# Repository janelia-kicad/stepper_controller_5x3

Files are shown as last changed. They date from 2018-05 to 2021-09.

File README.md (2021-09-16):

- [Repository Information](#org1390894)
  - [Description](#org5e8a07c)
- [Images](#org5d62455)
- [Schematic](#org4a582db)
- [Gerbers](#org312467b)
- [Bill of Materials](#org7a5552a)
  - [PCB Parts](#orgf9d748f)
  - [Supplemental Parts](#orgd5227c2)
  - [Vendor Parts Lists](#org4a799e8)
- [Supplemental Documentation](#org5107894)
  - [Assembly Instructions](#org090c8bb)

# Repository Information

-   **Name:** stepper\_controller\_5x3
-   **Version:** 1.3
-   **License:** Open-Source Hardware
-   **URL:** <https://github.com/janelia-kicad/stepper_controller_5x3>
-   **Author:** Peter Polidoro
-   **Email:** peter@polidoro.io

## Description

This board controls up to 3 stepper motors with optional forward and reverse limit switches for each motor.

# Images

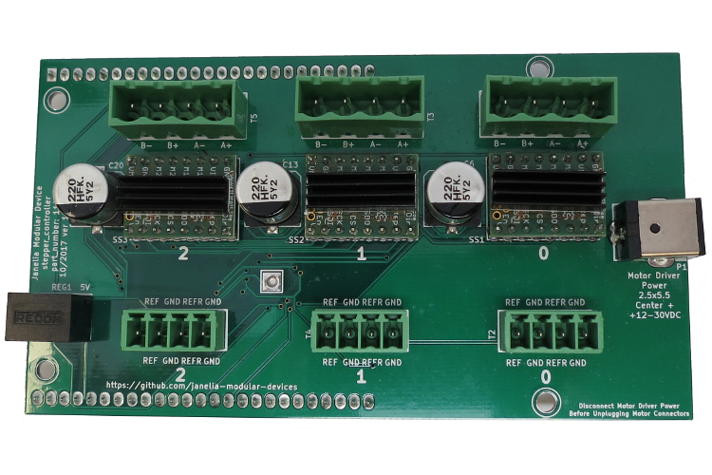
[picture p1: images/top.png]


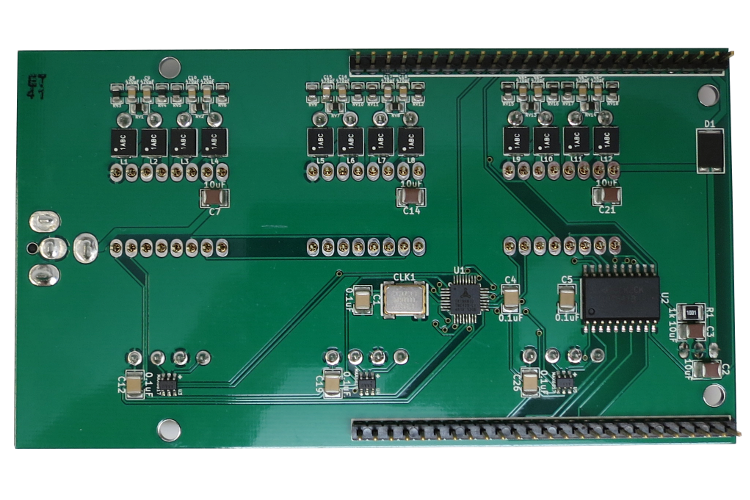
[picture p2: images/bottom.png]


# Schematic

[./schematic/stepper\_controller\_5x3.pdf](./schematic/stepper_controller_5x3.pdf)

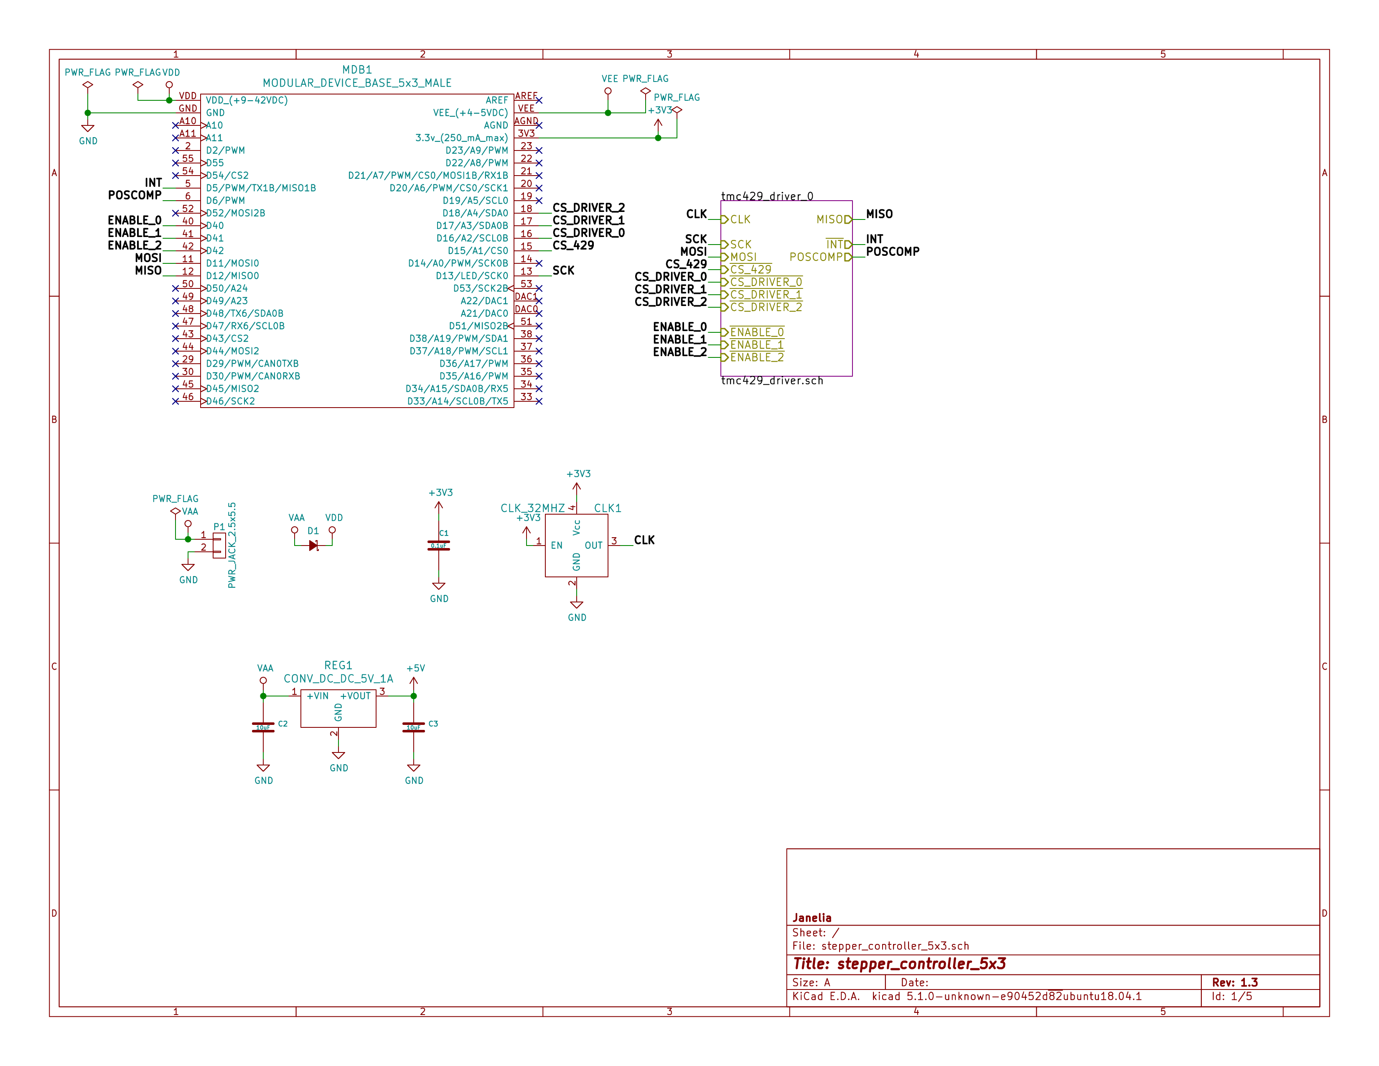
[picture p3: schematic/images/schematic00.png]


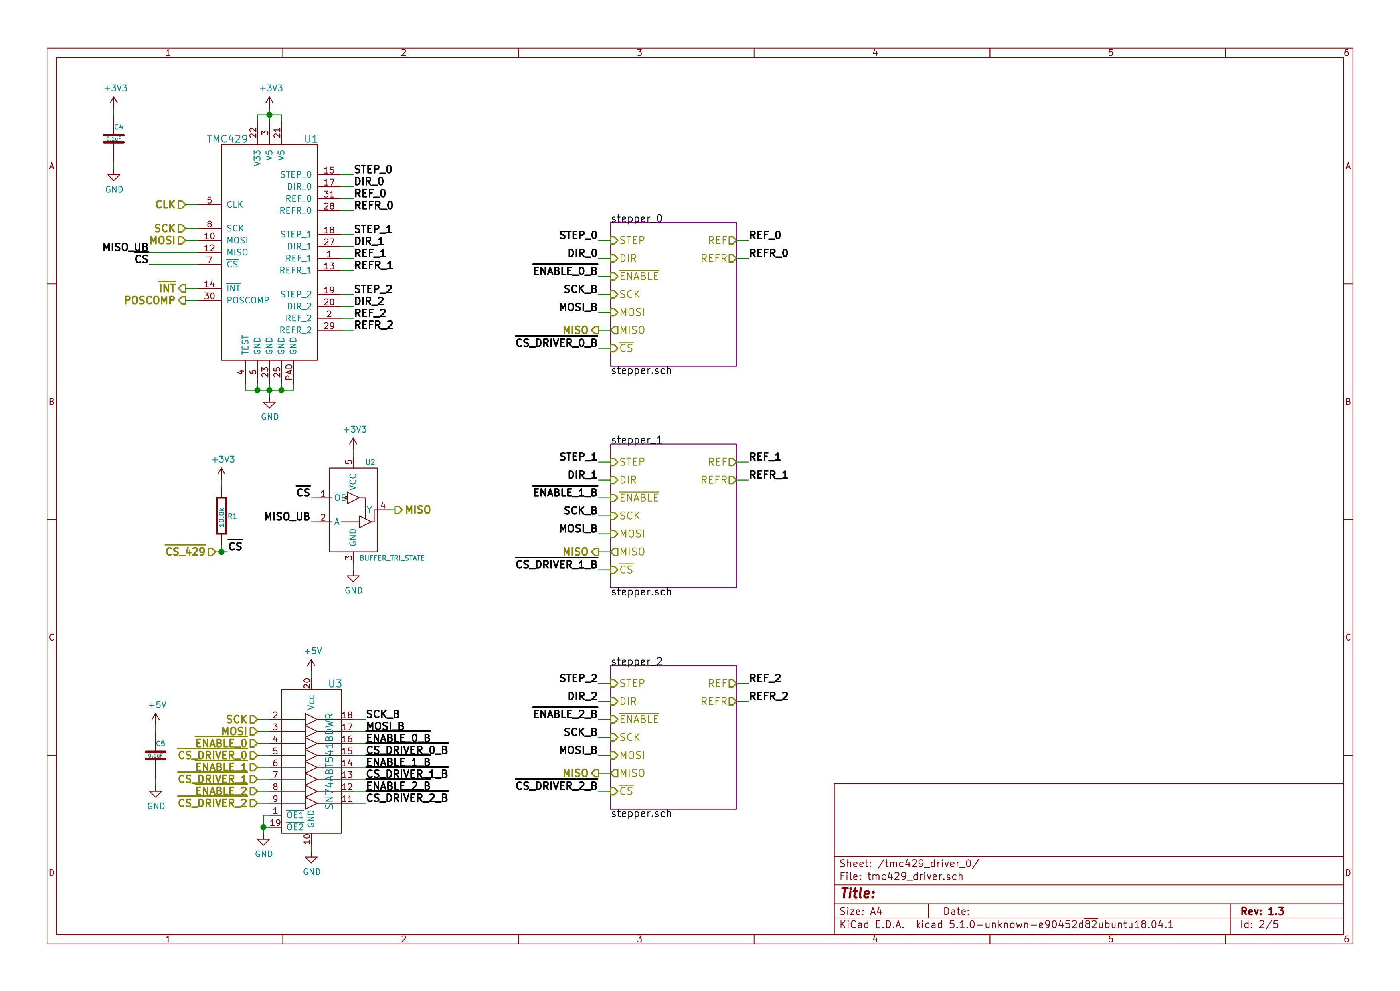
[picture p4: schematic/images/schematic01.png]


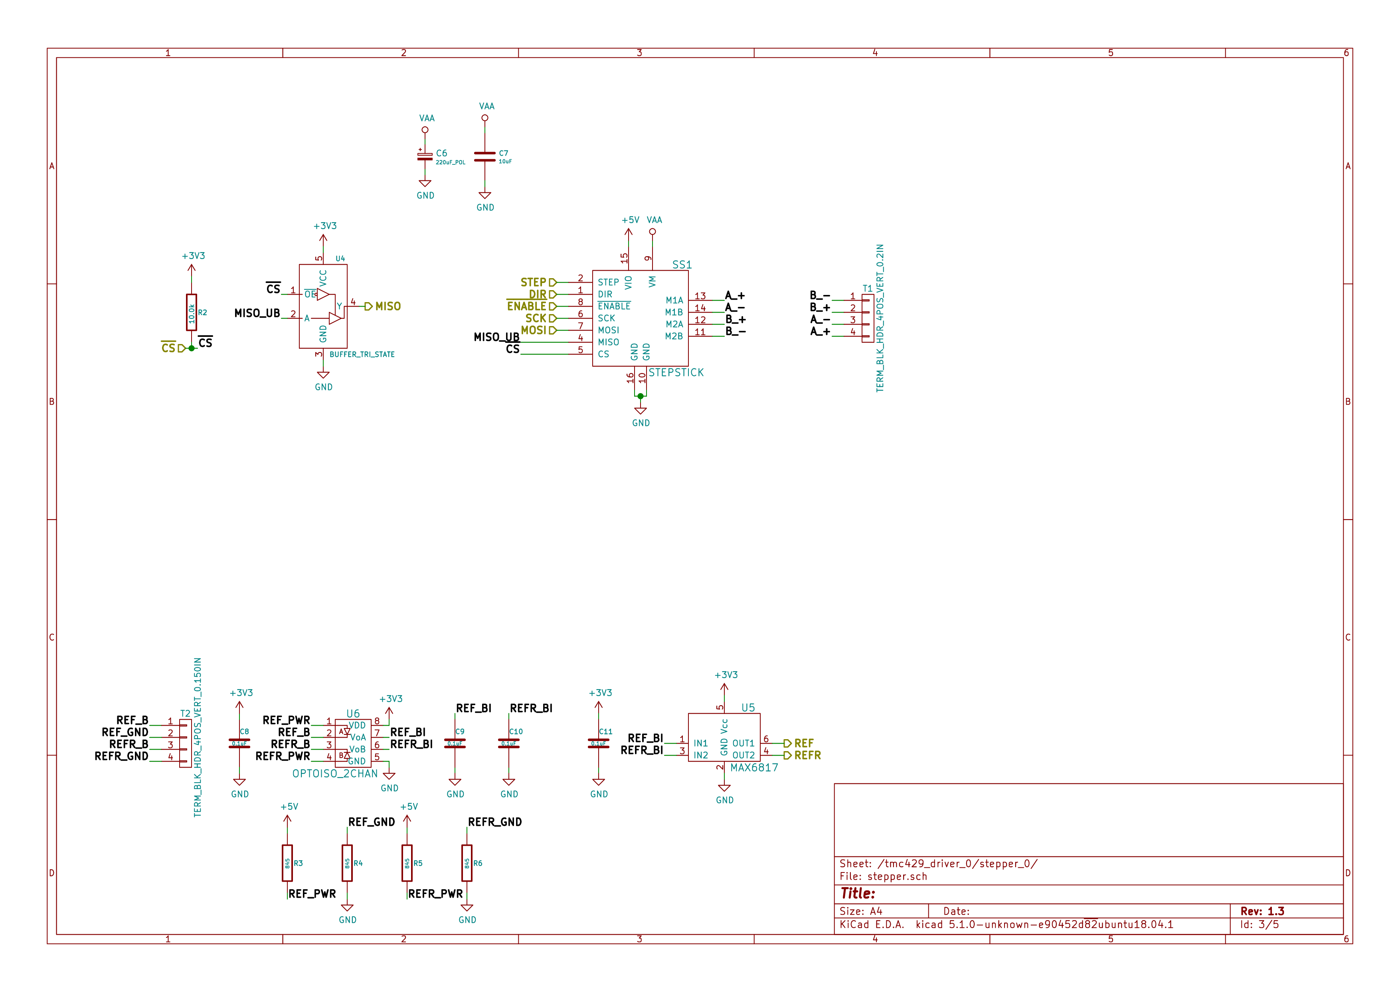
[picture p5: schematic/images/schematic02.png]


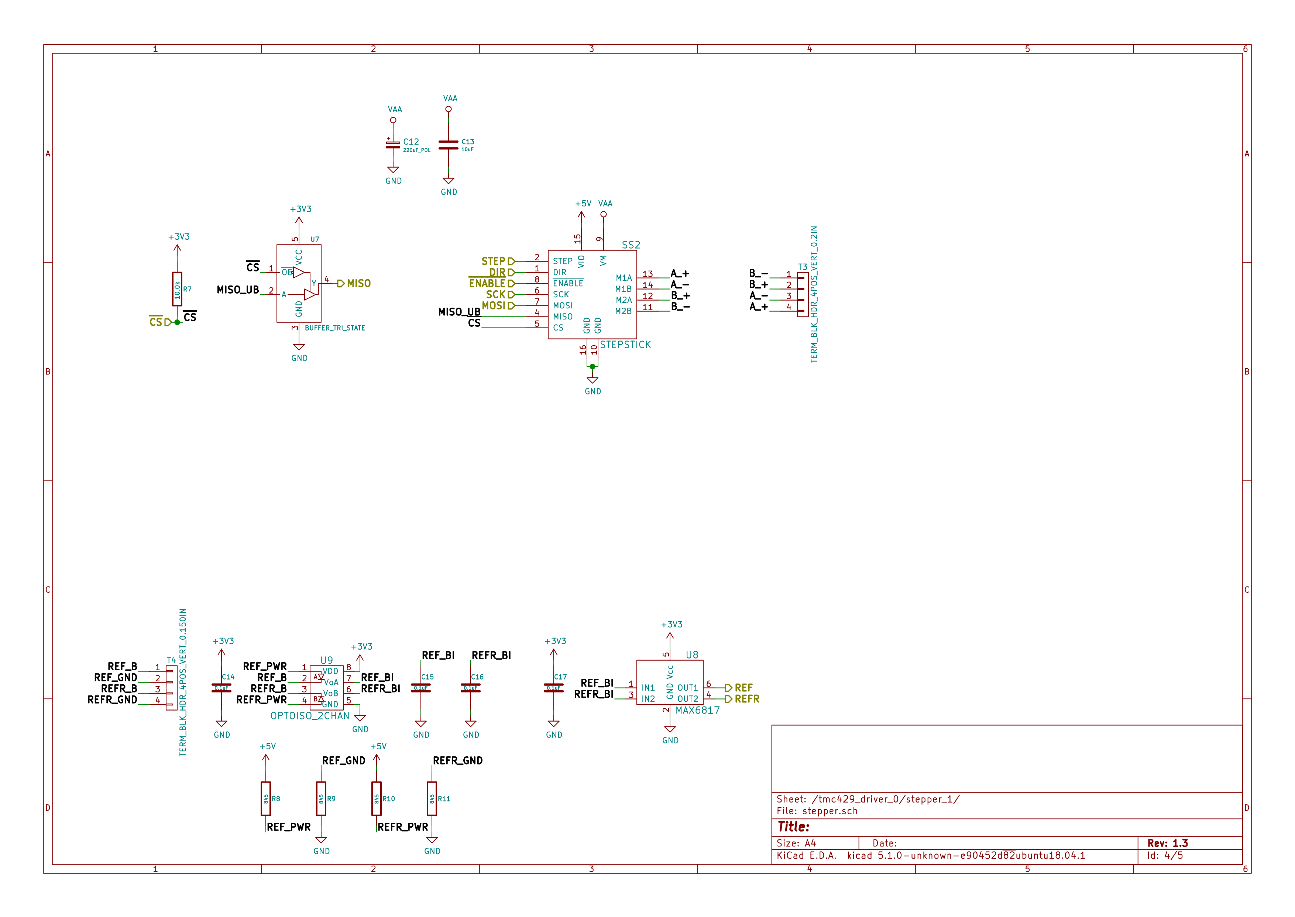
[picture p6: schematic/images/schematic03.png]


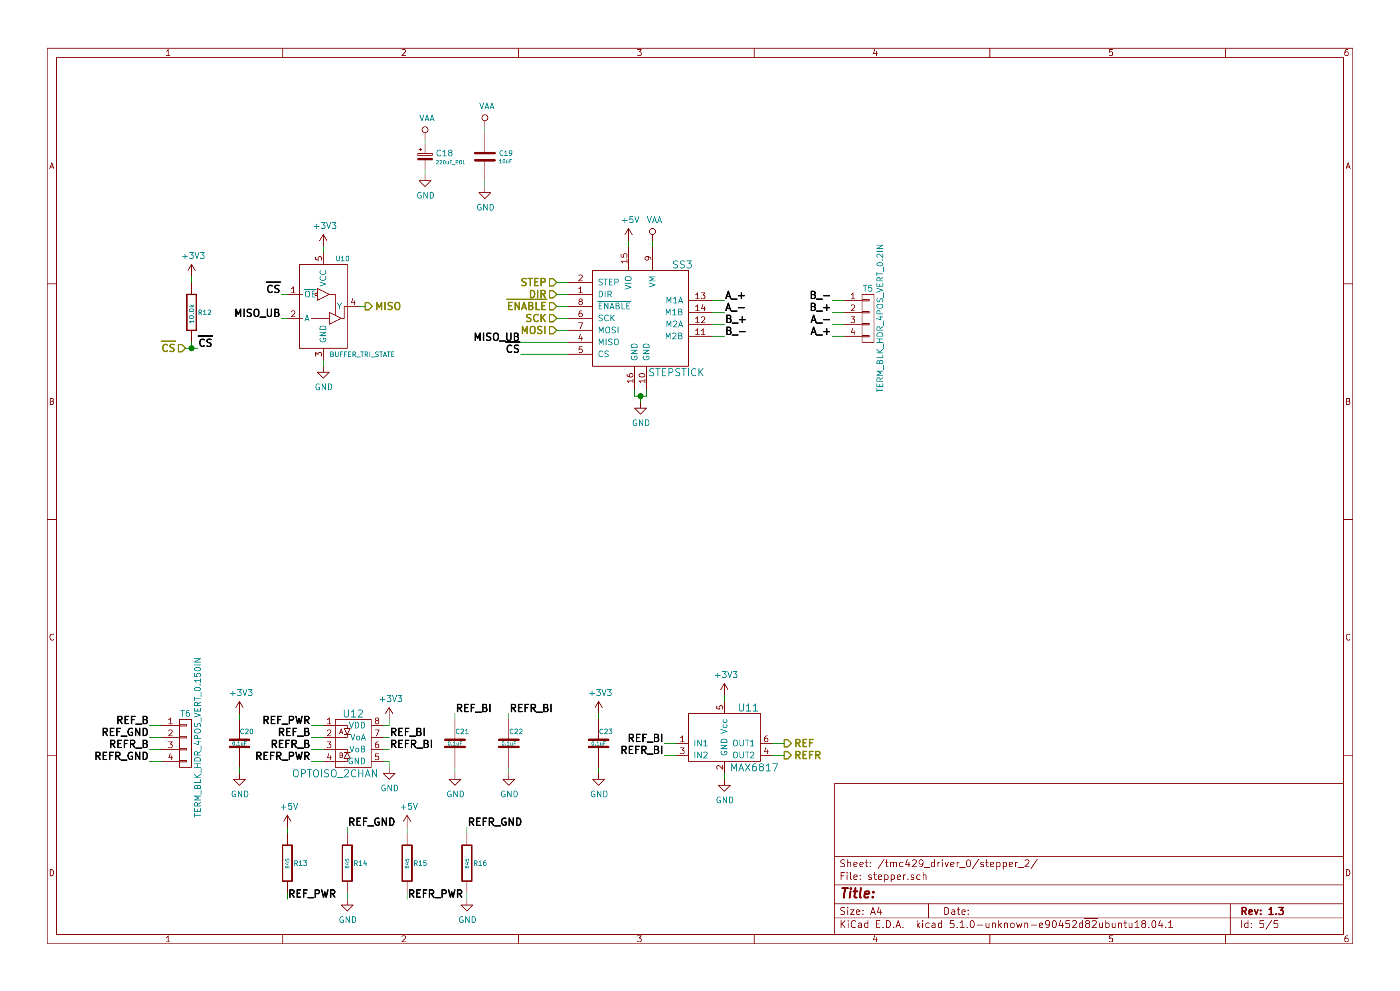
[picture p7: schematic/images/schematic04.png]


# Gerbers

Send gerbers zip file to your favorite PCB manufacturer for fabrication.

[./gerbers/stepper\_controller\_5x3\_v1.3.zip](./gerbers/stepper_controller_5x3_v1.3.zip)

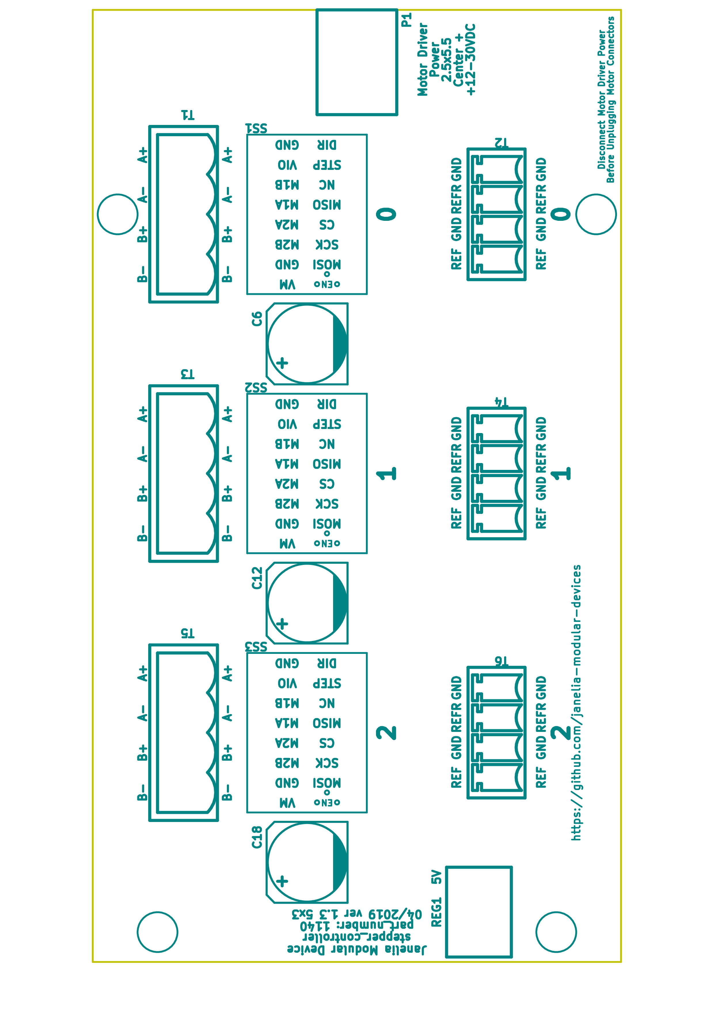
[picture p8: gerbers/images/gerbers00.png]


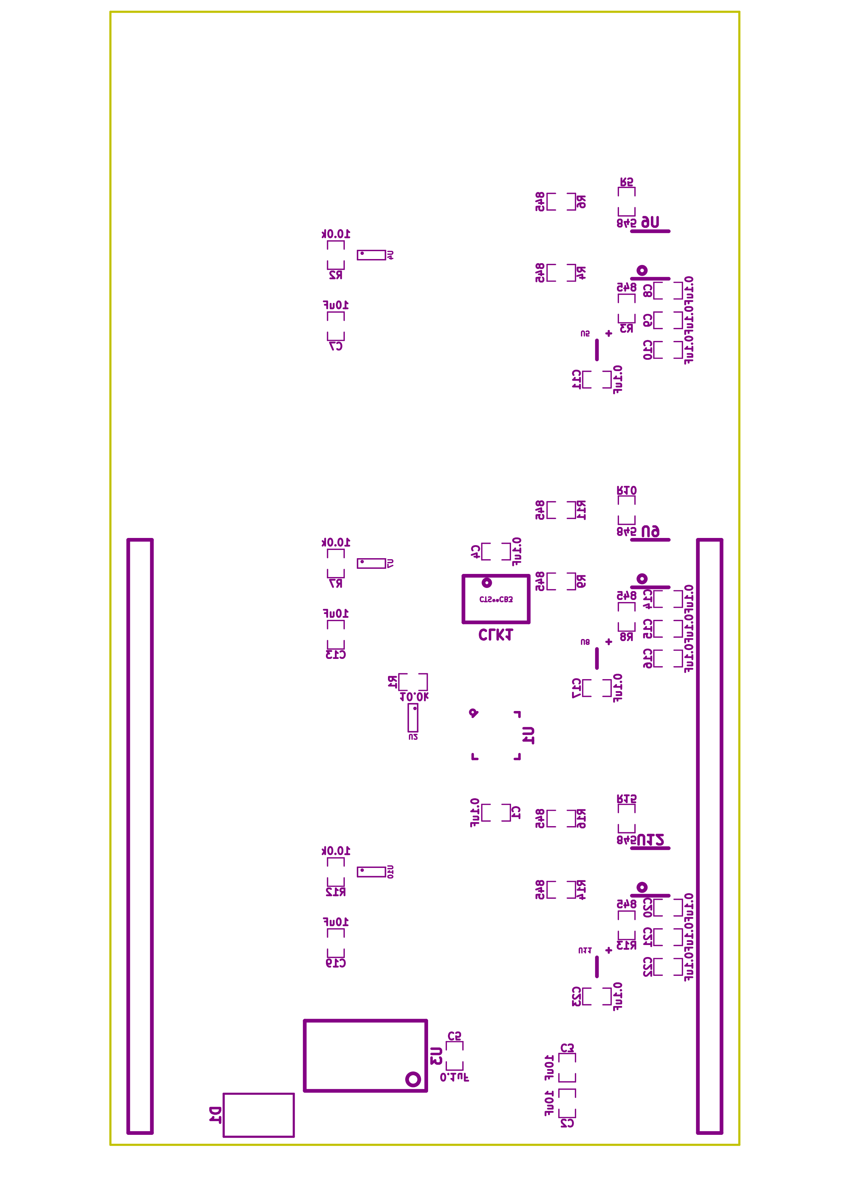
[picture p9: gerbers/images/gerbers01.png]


# Bill of Materials

## PCB Parts

| Item | Reference(s) | Quantity | PartNumber | Vendor  | Description |
|---- |--- |--- |--- |--- |--- |
| 1 | C1 C10 C11 C14 C15 C16 C17 C20 C21 C22 C23 C4 C5 C8 C9 | 15 | 399-14636-1-ND | digikey | CAP CER 0.1UF 50V X7R 0805 |
| 2 | C12 C18 C6 | 3 | PCE3812CT-ND | digikey | CAP ALUM 220UF 20% 50V SMD |
| 3 | C13 C19 C2 C3 C7 | 5 | 445-14419-1-ND | digikey | CAP CER 10UF 35V X5R 0805 |
| 4 | CLK1 | 1 | CTX277LVCT-ND | digikey | OSC XO 32.000MHZ HCMOS TTL SMD |
| 5 | D1 | 1 | 568-11697-1-ND | digikey | DIODE SCHOTTKY 45V 10A CFP15 |
| 6 | MDB1 | 2 | S1011E-25-ND | digikey | 25 Positions Header Breakaway Connector 0.1in |
| 7 | P1 | 1 | CP-063BH-ND | digikey | CONN PWR JACK DC 2.5X5.5 8A T/H |
| 8 | R1 R12 R2 R7 | 4 | P10.0KCCT-ND | digikey | RES SMD 10K OHM 1% 1/8W 0805 |
| 9 | R10 R11 R13 R14 R15 R16 R3 R4 R5 R6 R8 R9 | 12 | P845CCT-ND | digikey | RES SMD 845 OHM 1% 1/8W 0805 |
| 10 | REG1 | 1 | 945-1395-5-ND | digikey | CONV DC/DC 1A 5V OUT SIP VERT |
| 11 | SS1 SS2 SS3 | 48 | ED90331-ND | digikey | CONN PIN RCPT .025-.037 SOLDER |
| 12 | T1 T3 T5 | 3 | 277-1152-ND | digikey | TERM BLOCK HDR 4POS VERT 5.08MM |
| 13 | T2 T4 T6 | 3 | 277-1223-ND | digikey | TERM BLOCK HDR 4POS VERT 3.81MM |
| 14 | U1 | 1 | 1460-1071-1-ND | digikey | IC MOTOR CONTROLLER SPI 32QFN |
| 15 | U10 U2 U4 U7 | 4 | 296-11603-1-ND | digikey | IC BUF NON-INVERT 5.5V SOT23-5 |
| 16 | U11 U5 U8 | 3 | MAX6817EUT+TCT-ND | digikey | IC DEBOUNCER SWITCH DUAL SOT23-6 |
| 17 | U12 U6 U9 | 3 | 516-2614-1-ND | digikey | OPTOISO 3.75KV 2CH PUSH PULL 8SO |
| 18 | U3 | 1 | 296-14668-1-ND | digikey | Buffer Non-Inverting 1 Element 8 Bit per Element Push-Pull Output 20-SOIC |

## Supplemental Parts

| Item | Quantity | PartNumber | Vendor  | Description |
|---- |--- |--- |--- |--- |
| 1 | 3 | 277-1013-ND | digikey | TERM BLOCK PLUG 4POS STR 5.08MM |
| 2 | 3 | 277-1042-ND | digikey | TERM BLOCK PLUG 4POS 5.08MM |
| 3 | 3 | 277-1163-ND | digikey | TERM BLOCK PLUG 4POS STR 3.81MM |
| 4 | 3 | 277-1193-ND | digikey | TERM BLOCK PLUG 4POS 90DEG 3.81MM |
| 5 | 3 | 1460-1187-ND | digikey | TMC2130 STEPPER DRIVER BOARD |
| 6 | 3 | 501100B00000G-ND | digikey | HEATSINK 14-DIP/16-DIP |
| 7 | 1 | 3M10315-ND | digikey | TAPE ADHESIVE TRANSFER 1/2in X5YD |

## Vendor Parts Lists

[./bom/digikey\_parts.csv](./bom/digikey_parts.csv)

[./bom/supplemental\_digikey\_parts.csv](./bom/supplemental_digikey_parts.csv)

# Supplemental Documentation

## Assembly Instructions

-   Solder header pins into the stepper driver board(s), making note of TOP label. Insert header pins on bottom of board so that the long unsoldered header pins point down when the TOP label faces up.
-   Expose one side of the thermal adhesive tape and attach to the bottom of the heatsink. Trim tape so it does not extend beyond heatsink edges.
-   Expose the other side of the thermal adhesive tape and attach the heatsink to the stepper driver board on the side with the TOP label.
-   Solder surface mount and through hole components onto the pcb.
-   Insert stepper driver board(s) into pin receptacles.

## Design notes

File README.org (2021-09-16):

# Created 2019-04-11 Thu 14:58
#+OPTIONS: title:nil author:nil email:nil toc:t |:t ^:nil
* Repository Information

- Name :: stepper_controller_5x3
- Version :: 1.3
- License :: Open-Source Hardware
- URL :: https://github.com/janelia-kicad/stepper_controller_5x3
- Author :: Peter Polidoro
- Email :: peter@polidoro.io

** Description

This board controls up to 3 stepper motors with optional forward and reverse
limit switches for each motor.

* Images





* Schematic

[[file:./schematic/stepper_controller_5x3.pdf][./schematic/stepper_controller_5x3.pdf]]











* Gerbers

Send gerbers zip file to your favorite PCB manufacturer for fabrication.

[[file:./gerbers/stepper_controller_5x3_v1.3.zip][./gerbers/stepper_controller_5x3_v1.3.zip]]





* Bill of Materials

** PCB Parts

| Item | Reference(s)                                           | Quantity | PartNumber        | Vendor  | Description                                                               |
|------+--------------------------------------------------------+----------+-------------------+---------+---------------------------------------------------------------------------|
|    1 | C1 C10 C11 C14 C15 C16 C17 C20 C21 C22 C23 C4 C5 C8 C9 |       15 | 399-14636-1-ND    | digikey | CAP CER 0.1UF 50V X7R 0805                                                |
|    2 | C12 C18 C6                                             |        3 | PCE3812CT-ND      | digikey | CAP ALUM 220UF 20% 50V SMD                                                |
|    3 | C13 C19 C2 C3 C7                                       |        5 | 445-14419-1-ND    | digikey | CAP CER 10UF 35V X5R 0805                                                 |
|    4 | CLK1                                                   |        1 | CTX277LVCT-ND     | digikey | OSC XO 32.000MHZ HCMOS TTL SMD                                            |
|    5 | D1                                                     |        1 | 568-11697-1-ND    | digikey | DIODE SCHOTTKY 45V 10A CFP15                                              |
|    6 | MDB1                                                   |        2 | S1011E-25-ND      | digikey | 25 Positions Header Breakaway Connector 0.1in                             |
|    7 | P1                                                     |        1 | CP-063BH-ND       | digikey | CONN PWR JACK DC 2.5X5.5 8A T/H                                           |
|    8 | R1 R12 R2 R7                                           |        4 | P10.0KCCT-ND      | digikey | RES SMD 10K OHM 1% 1/8W 0805                                              |
|    9 | R10 R11 R13 R14 R15 R16 R3 R4 R5 R6 R8 R9              |       12 | P845CCT-ND        | digikey | RES SMD 845 OHM 1% 1/8W 0805                                              |
|   10 | REG1                                                   |        1 | 945-1395-5-ND     | digikey | CONV DC/DC 1A 5V OUT SIP VERT                                             |
|   11 | SS1 SS2 SS3                                            |       48 | ED90331-ND        | digikey | CONN PIN RCPT .025-.037 SOLDER                                            |
|   12 | T1 T3 T5                                               |        3 | 277-1152-ND       | digikey | TERM BLOCK HDR 4POS VERT 5.08MM                                           |
|   13 | T2 T4 T6                                               |        3 | 277-1223-ND       | digikey | TERM BLOCK HDR 4POS VERT 3.81MM                                           |
|   14 | U1                                                     |        1 | 1460-1071-1-ND    | digikey | IC MOTOR CONTROLLER SPI 32QFN                                             |
|   15 | U10 U2 U4 U7                                           |        4 | 296-11603-1-ND    | digikey | IC BUF NON-INVERT 5.5V SOT23-5                                            |
|   16 | U11 U5 U8                                              |        3 | MAX6817EUT+TCT-ND | digikey | IC DEBOUNCER SWITCH DUAL SOT23-6                                          |
|   17 | U12 U6 U9                                              |        3 | 516-2614-1-ND     | digikey | OPTOISO 3.75KV 2CH PUSH PULL 8SO                                          |
|   18 | U3                                                     |        1 | 296-14668-1-ND    | digikey | Buffer Non-Inverting 1 Element 8 Bit per Element Push-Pull Output 20-SOIC |

** Supplemental Parts

| Item | Quantity | PartNumber       | Vendor  | Description                       |
|------+----------+------------------+---------+-----------------------------------|
|    1 |        3 | 277-1013-ND      | digikey | TERM BLOCK PLUG 4POS STR 5.08MM   |
|    2 |        3 | 277-1042-ND      | digikey | TERM BLOCK PLUG 4POS 5.08MM       |
|    3 |        3 | 277-1163-ND      | digikey | TERM BLOCK PLUG 4POS STR 3.81MM   |
|    4 |        3 | 277-1193-ND      | digikey | TERM BLOCK PLUG 4POS 90DEG 3.81MM |
|    5 |        3 | 1460-1187-ND     | digikey | TMC2130 STEPPER DRIVER BOARD      |
|    6 |        3 | 501100B00000G-ND | digikey | HEATSINK 14-DIP/16-DIP            |
|    7 |        1 | 3M10315-ND       | digikey | TAPE ADHESIVE TRANSFER 1/2in X5YD |

** Vendor Parts Lists

[[file:./bom/digikey_parts.csv][./bom/digikey_parts.csv]]

[[file:./bom/supplemental_digikey_parts.csv][./bom/supplemental_digikey_parts.csv]]

* Supplemental Documentation

** Assembly Instructions

- Solder header pins into the stepper driver board(s), making note of TOP label.
  Insert header pins on bottom of board so that the long unsoldered header
  pins point down when the TOP label faces up.
- Expose one side of the thermal adhesive tape and attach to the bottom of the
  heatsink. Trim tape so it does not extend beyond heatsink edges.
- Expose the other side of the thermal adhesive tape and attach the heatsink
  to the stepper driver board on the side with the TOP label.
- Solder surface mount and through hole components onto the pcb.
- Insert stepper driver board(s) into pin receptacles.

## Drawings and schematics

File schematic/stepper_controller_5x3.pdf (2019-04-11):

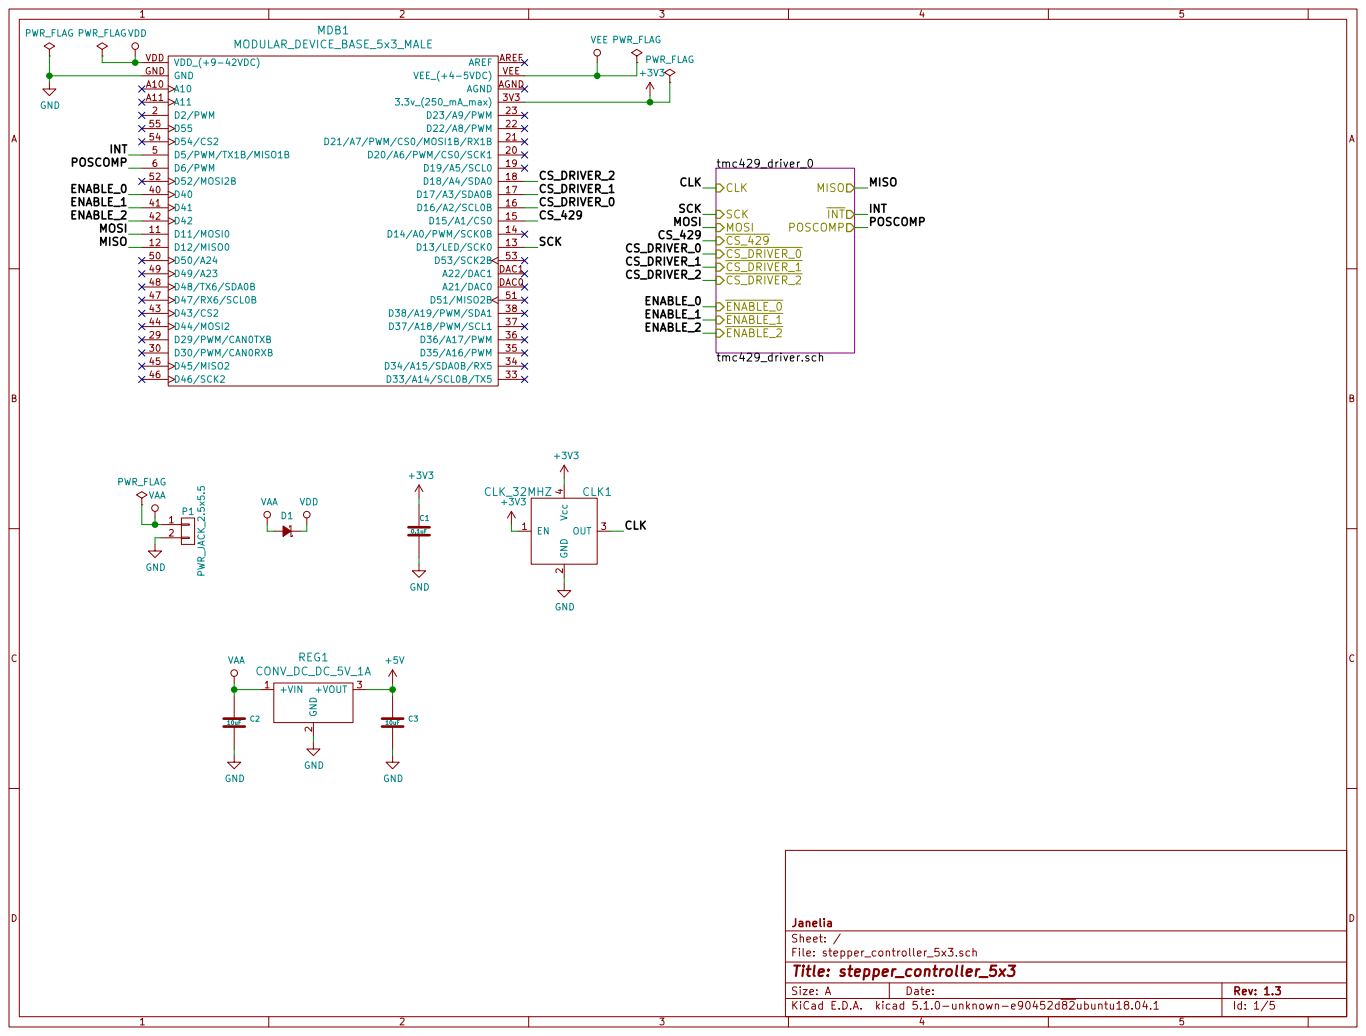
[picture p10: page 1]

File: stepper_controller_5x3.sch Sheet: / Janelia

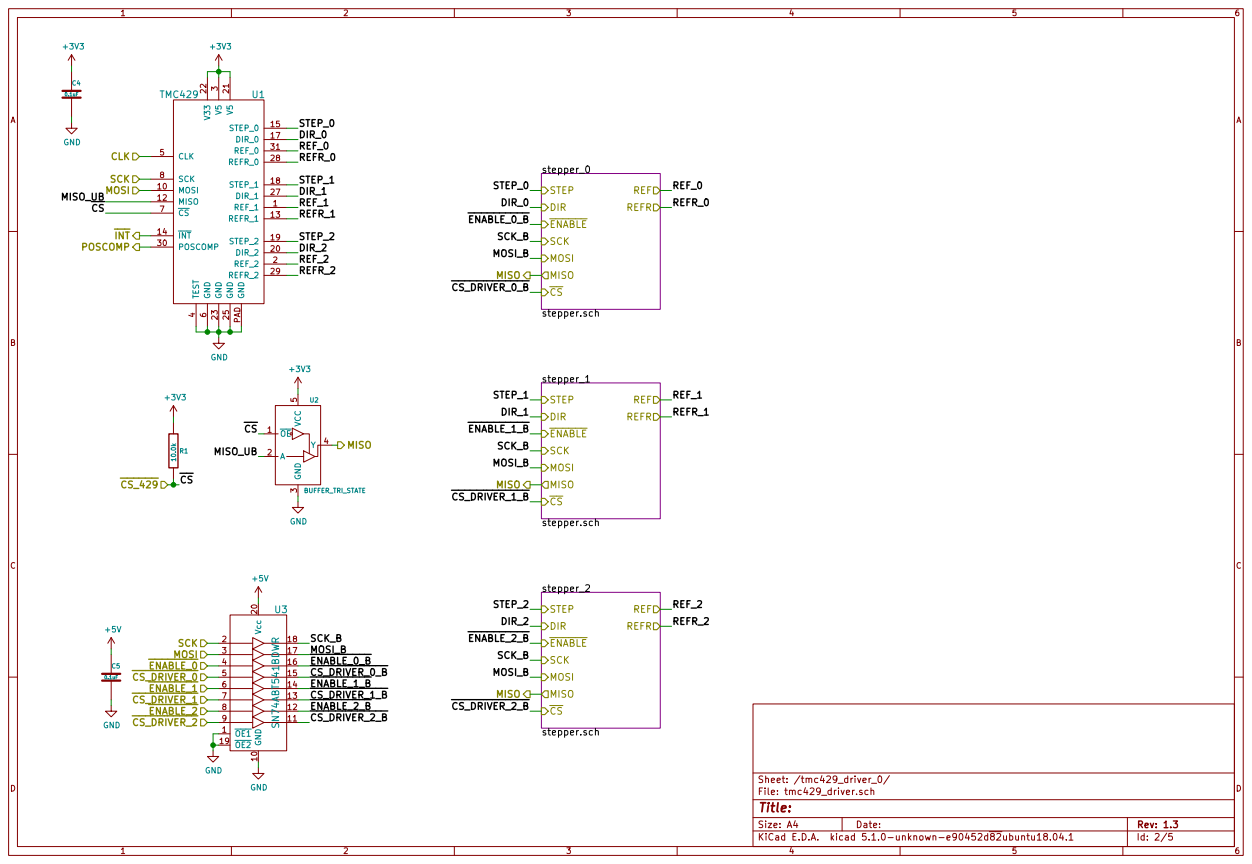
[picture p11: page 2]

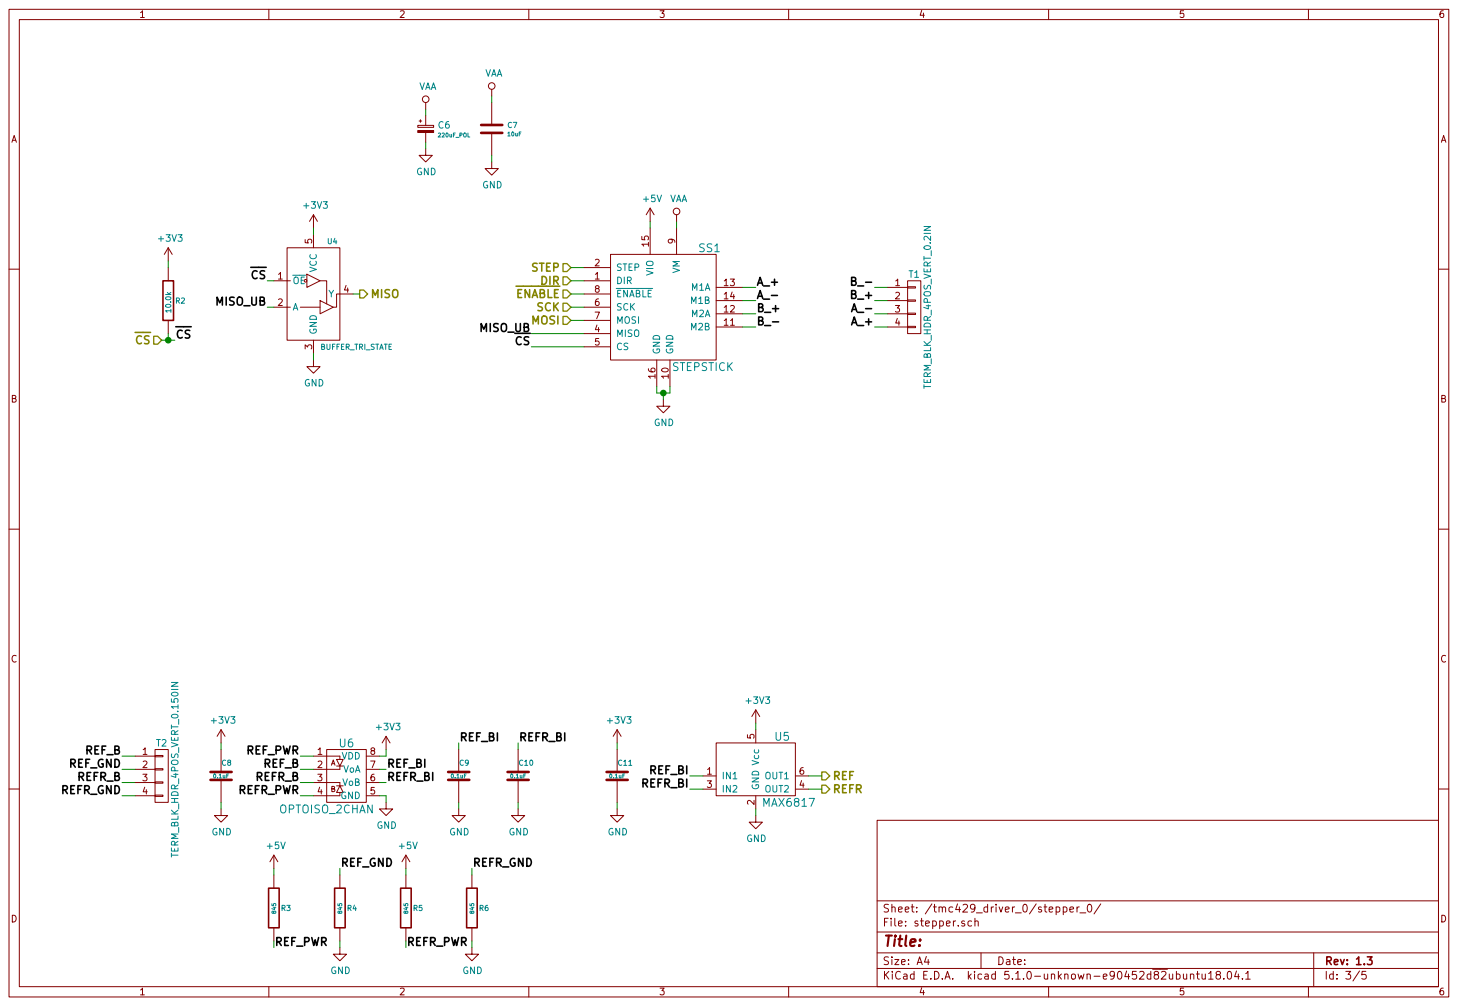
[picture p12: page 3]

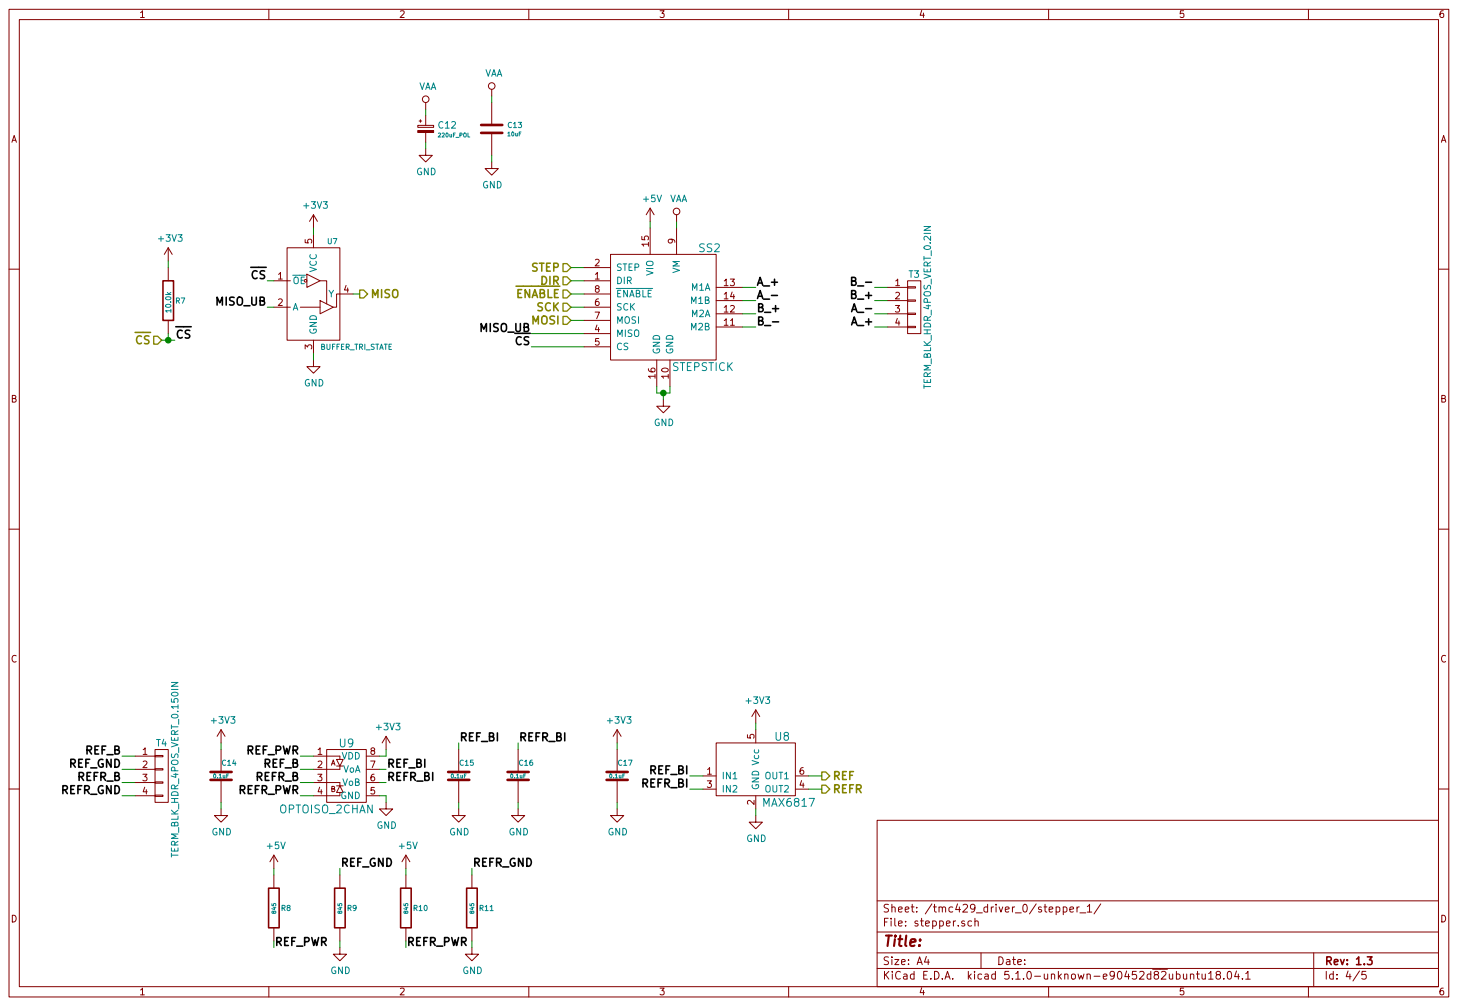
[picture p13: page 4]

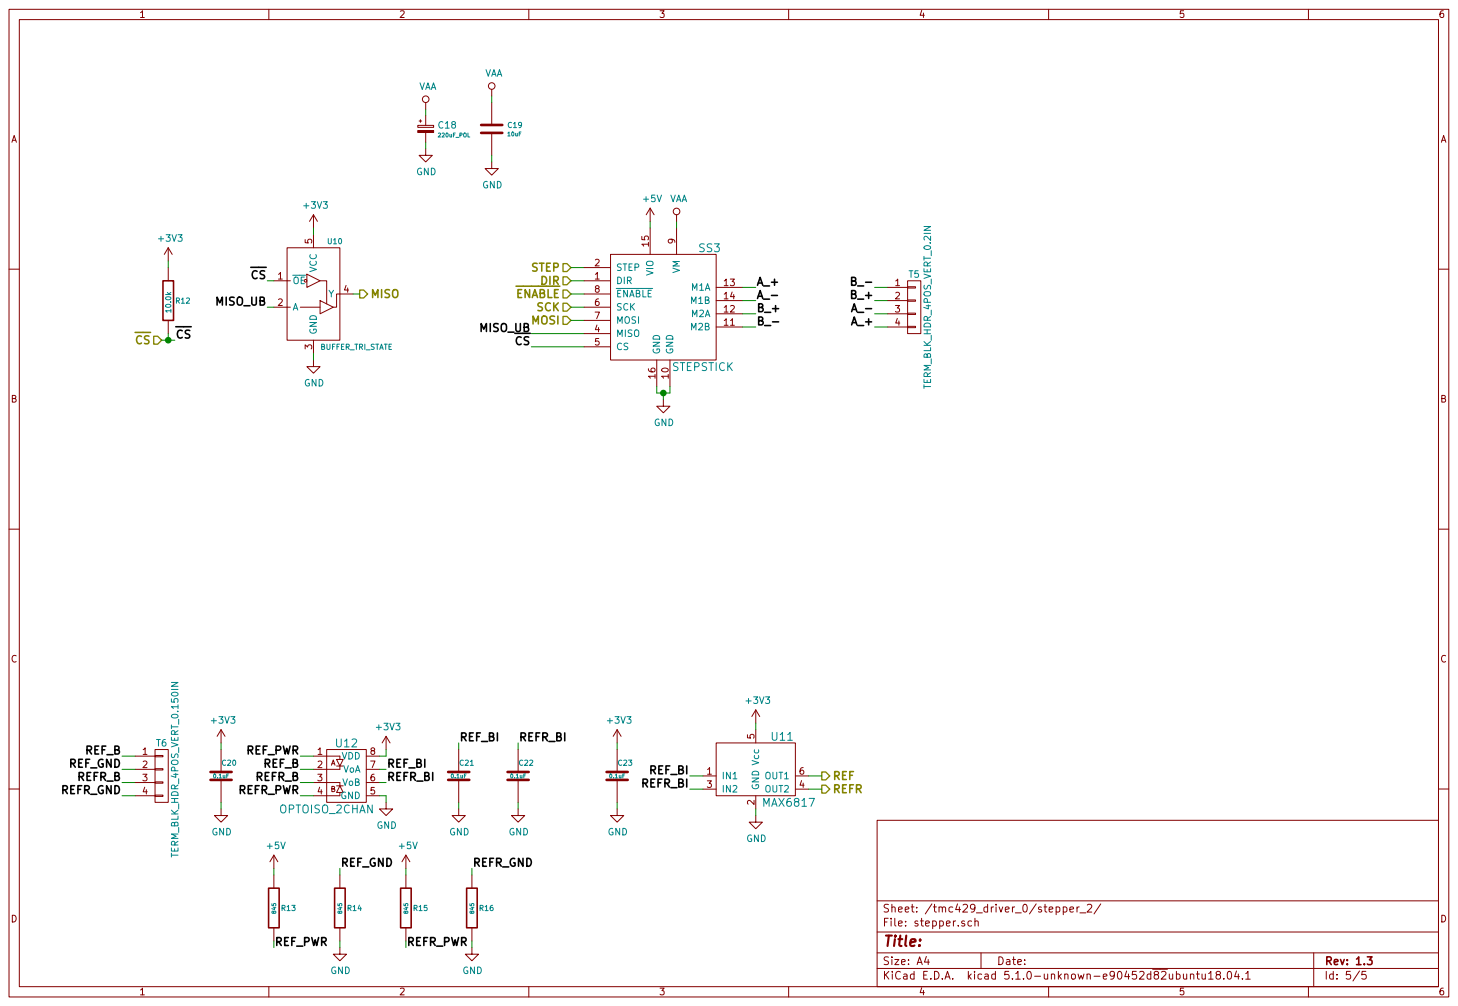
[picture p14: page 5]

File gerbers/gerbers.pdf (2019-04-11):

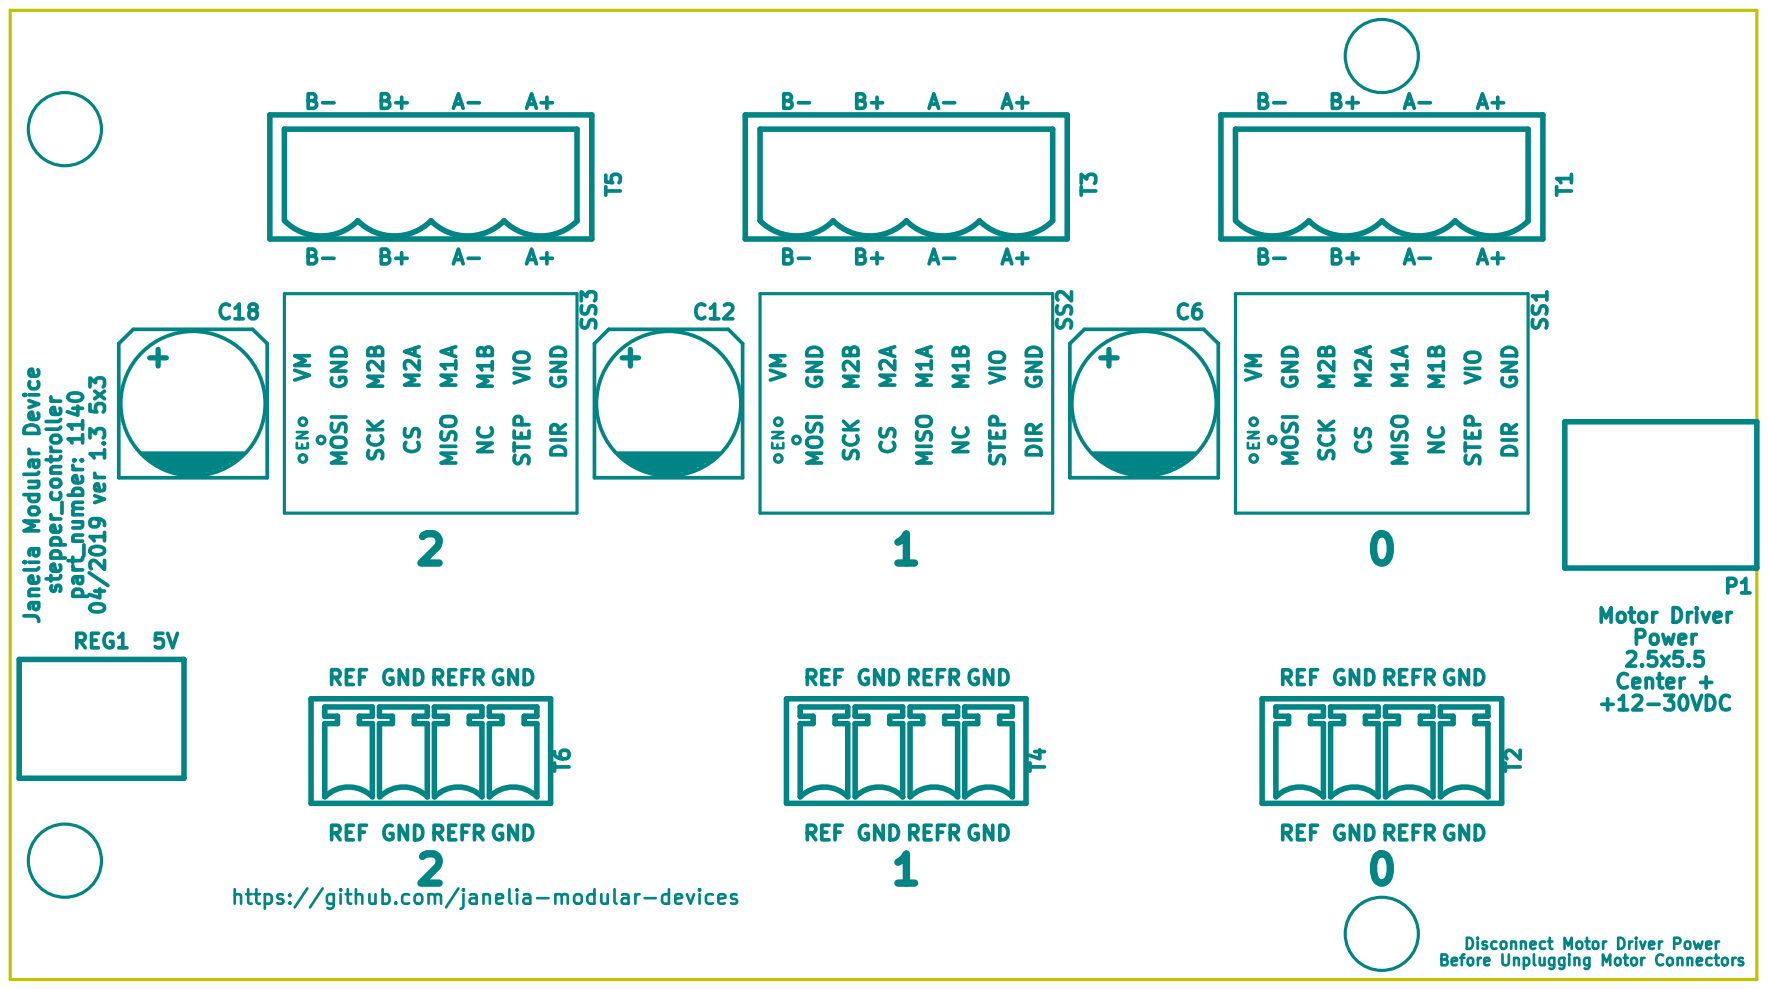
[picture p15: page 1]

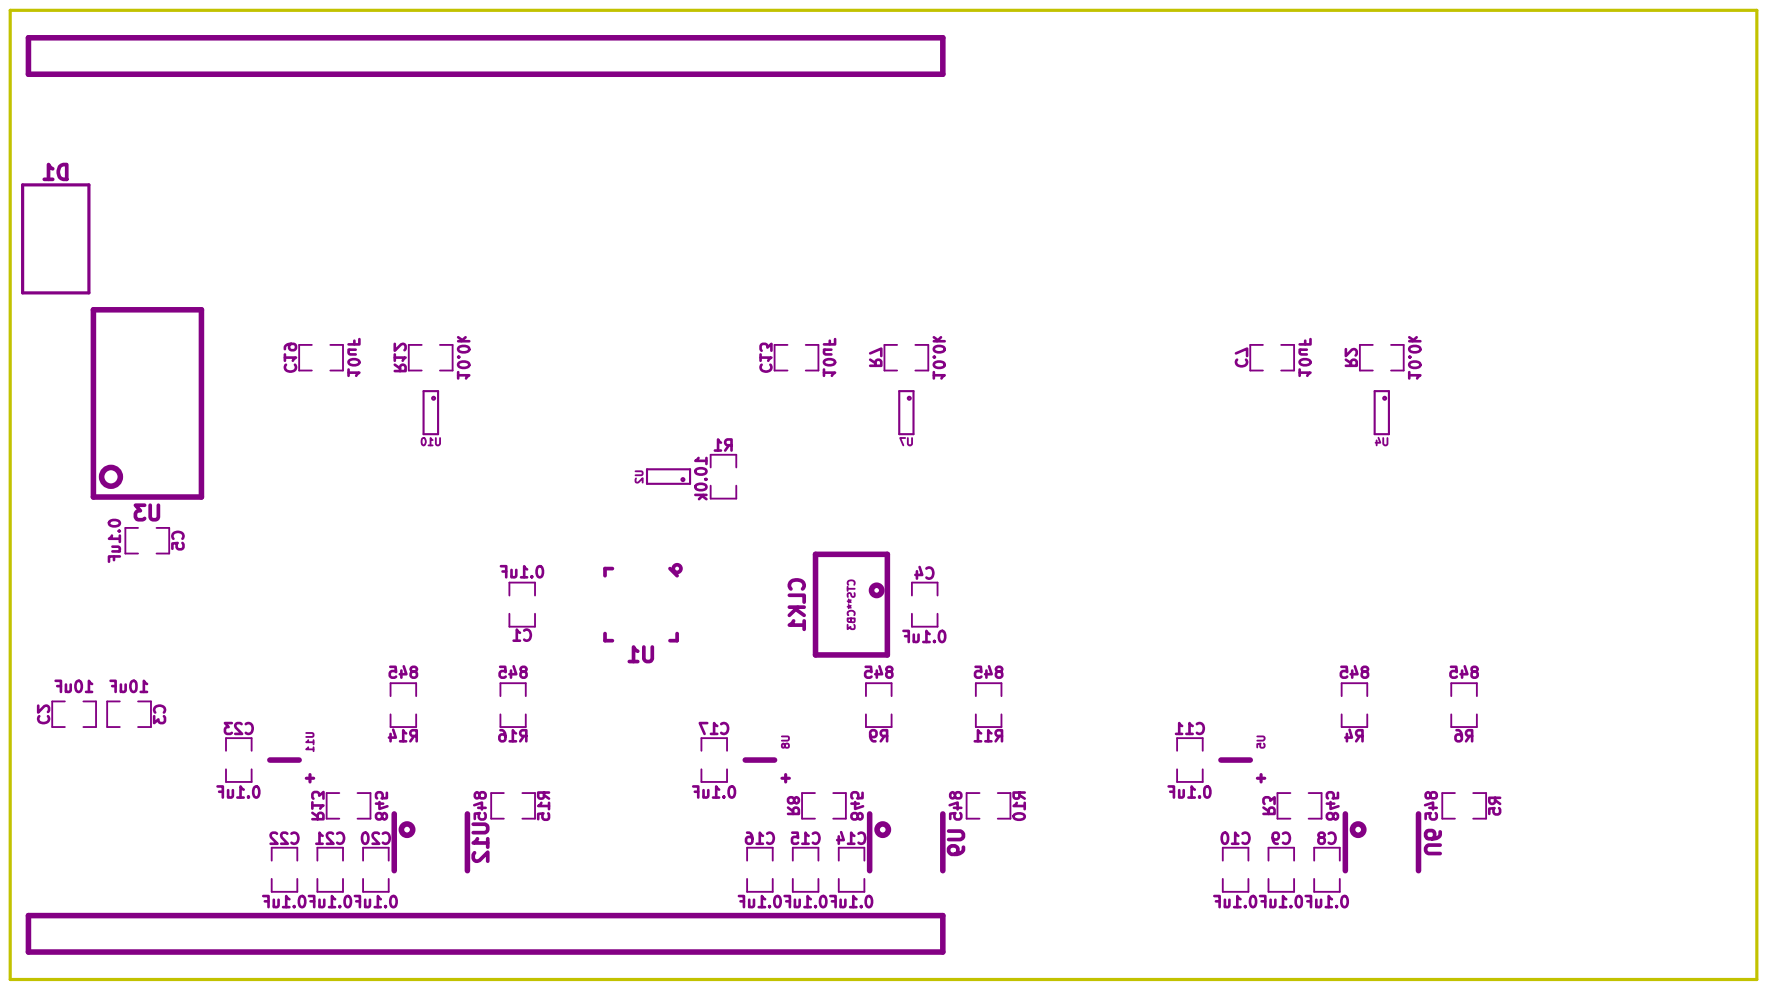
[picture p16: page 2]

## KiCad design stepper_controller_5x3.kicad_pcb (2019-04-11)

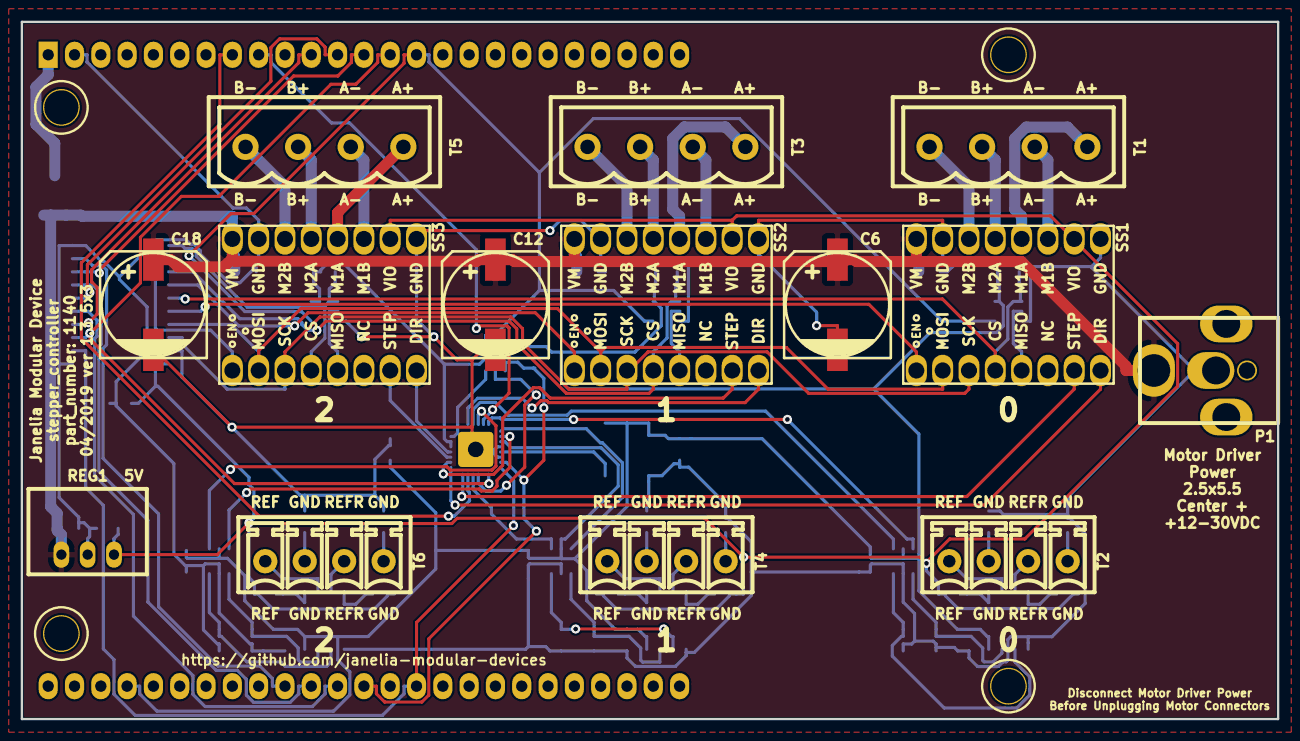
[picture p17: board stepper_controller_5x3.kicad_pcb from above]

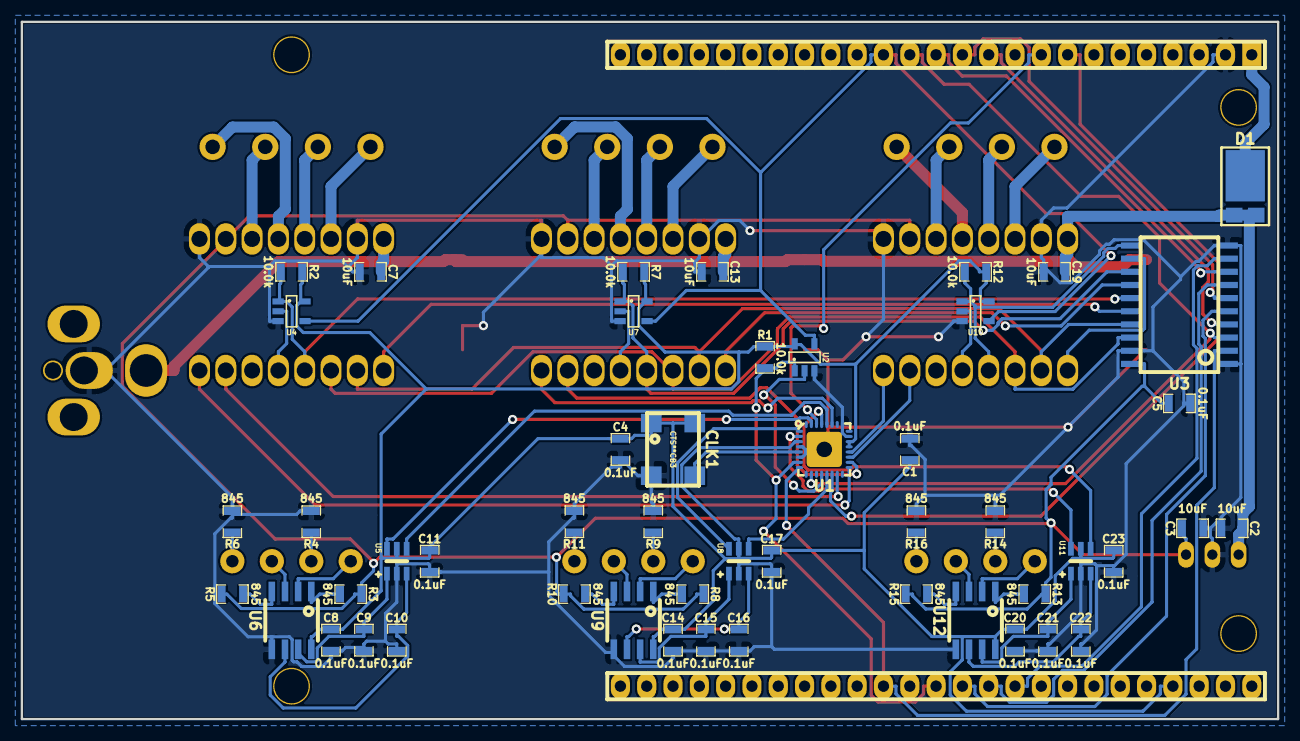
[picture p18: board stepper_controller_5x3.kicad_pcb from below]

Board: 2 copper layers, 121.3 x 67.3 mm, 65 parts (50 on the bottom side), 78 nets.

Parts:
C1, C4, C5, C8, C9, C10, C11, C14, C15, C16, C17, C20, C21, C22, C23: 0.1uF; SM0805
C2, C3, C7, C13, C19: 10uF; SM0805
C6, C12, C18: 220uF_POL; C_ELEC_10
CLK1: CLK_32MHZ; CTS_SMD_4_7X5MM
D1: diode_schottky_45V_10A; CFP15
MDB1: MODULAR_DEVICE_BASE_5x3_MALE; MODULAR_DEVICE_BASE_5X3_MALE
P1: PWR_JACK_2.5x5.5; DCJACK_2PIN_HIGHCURRENT
R1, R2, R7, R12: 10.0k; SM0805
R3, R4, R5, R6, R8, R9, R10, R11, R13, R14, R15, R16: 845; SM0805
REG1: CONV_DC_DC_5V_1A; DC_DC_CONV_R78C
SS1, SS2, SS3: STEPSTICK
T1, T3, T5: TERM_BLK_HDR_4POS_VERT_0.2IN
T2, T4, T6: TERM_BLK_HDR_4POS_VERT_0.150IN
U1: TMC429; QFN-5x5-32
U2, U4, U7, U10: BUFFER_TRI_STATE; SOT-23-5
U3: SN74ABT541BDWR; SOIC_20
U5, U8, U11: MAX6817
U6, U9, U12: OPTOISO_2CHAN; SO-8

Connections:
+3V3: C1.1, C4.1, C8.1, C11.1, C14.1, C17.1, C20.1, C23.1, CLK1.1, CLK1.4, MDB1.3V3, R1.1, R2.1, R7.1, R12.1, U1.3, U1.21, U1.22, U2.5, U4.5, U5.5, U6.8, U7.5, U8.5, U9.8, U10.5, U11.5, U12.8
+5V: C3.1, C5.1, R3.1, R5.1, R8.1, R10.1, R13.1, R15.1, REG1.3, SS1.15, SS2.15, SS3.15, U3.20
/CLK: CLK1.3, U1.5
/CS_429: MDB1.15, R1.2, U1.7, U2.1
/CS_DRIVER_0: MDB1.16, U3.5
/CS_DRIVER_1: MDB1.17, U3.7
/CS_DRIVER_2: MDB1.18, U3.9
/ENABLE_0: MDB1.40, U3.4
/ENABLE_1: MDB1.41, U3.6
/ENABLE_2: MDB1.42, U3.8
/INT: MDB1.5, U1.14
/MISO: MDB1.12, U2.4, U4.4, U7.4, U10.4
/MOSI: MDB1.11, U1.10, U3.3
/POSCOMP: MDB1.6, U1.30
/SCK: MDB1.13, U1.8, U3.2
/tmc429_driver_0/DIR_0: SS1.1, U1.17
/tmc429_driver_0/DIR_1: SS2.1, U1.27
/tmc429_driver_0/DIR_2: SS3.1, U1.20
/tmc429_driver_0/MISO_UB: U1.12, U2.2
/tmc429_driver_0/MOSI_B: SS1.7, SS2.7, SS3.7, U3.17
/tmc429_driver_0/REFR_0: U1.28, U5.4
/tmc429_driver_0/REFR_1: U1.13, U8.4
/tmc429_driver_0/REFR_2: U1.29, U11.4
/tmc429_driver_0/REF_0: U1.31, U5.6
/tmc429_driver_0/REF_1: U1.1, U8.6
/tmc429_driver_0/REF_2: U1.2, U11.6
/tmc429_driver_0/SCK_B: SS1.6, SS2.6, SS3.6, U3.18
/tmc429_driver_0/STEP_0: SS1.2, U1.15
/tmc429_driver_0/STEP_1: SS2.2, U1.18
/tmc429_driver_0/STEP_2: SS3.2, U1.19
/tmc429_driver_0/stepper_0/A_+: SS1.13, T1.4
/tmc429_driver_0/stepper_0/A_-: SS1.14, T1.3
/tmc429_driver_0/stepper_0/B_+: SS1.12, T1.2
/tmc429_driver_0/stepper_0/B_-: SS1.11, T1.1
/tmc429_driver_0/stepper_0/MISO_UB: SS1.4, U4.2
/tmc429_driver_0/stepper_0/REFR_B: T2.3, U6.3
/tmc429_driver_0/stepper_0/REFR_BI: C10.1, U5.3, U6.6
/tmc429_driver_0/stepper_0/REFR_GND: R6.1, T2.4
/tmc429_driver_0/stepper_0/REFR_PWR: R5.2, U6.4
/tmc429_driver_0/stepper_0/REF_B: T2.1, U6.2
/tmc429_driver_0/stepper_0/REF_BI: C9.1, U5.1, U6.7
/tmc429_driver_0/stepper_0/REF_GND: R4.1, T2.2
/tmc429_driver_0/stepper_0/REF_PWR: R3.2, U6.1
/tmc429_driver_0/stepper_1/A_+: SS2.13, T3.4
/tmc429_driver_0/stepper_1/A_-: SS2.14, T3.3
/tmc429_driver_0/stepper_1/B_+: SS2.12, T3.2
/tmc429_driver_0/stepper_1/B_-: SS2.11, T3.1
/tmc429_driver_0/stepper_1/MISO_UB: SS2.4, U7.2
/tmc429_driver_0/stepper_1/REFR_B: T4.3, U9.3
/tmc429_driver_0/stepper_1/REFR_BI: C16.1, U8.3, U9.6
/tmc429_driver_0/stepper_1/REFR_GND: R11.1, T4.4
/tmc429_driver_0/stepper_1/REFR_PWR: R10.2, U9.4
/tmc429_driver_0/stepper_1/REF_B: T4.1, U9.2
/tmc429_driver_0/stepper_1/REF_BI: C15.1, U8.1, U9.7
/tmc429_driver_0/stepper_1/REF_GND: R9.1, T4.2
/tmc429_driver_0/stepper_1/REF_PWR: R8.2, U9.1
/tmc429_driver_0/stepper_2/A_+: SS3.13, T5.4
/tmc429_driver_0/stepper_2/A_-: SS3.14, T5.3
/tmc429_driver_0/stepper_2/B_+: SS3.12, T5.2
/tmc429_driver_0/stepper_2/B_-: SS3.11, T5.1
/tmc429_driver_0/stepper_2/MISO_UB: SS3.4, U10.2
/tmc429_driver_0/stepper_2/REFR_B: T6.3, U12.3
/tmc429_driver_0/stepper_2/REFR_BI: C22.1, U11.3, U12.6
/tmc429_driver_0/stepper_2/REFR_GND: R16.1, T6.4
/tmc429_driver_0/stepper_2/REFR_PWR: R15.2, U12.4
/tmc429_driver_0/stepper_2/REF_B: T6.1, U12.2
/tmc429_driver_0/stepper_2/REF_BI: C21.1, U11.1, U12.7
/tmc429_driver_0/stepper_2/REF_GND: R14.1, T6.2
/tmc429_driver_0/stepper_2/REF_PWR: R13.2, U12.1
/tmc429_driver_0/~CS_DRIVER_0_B: R2.2, SS1.5, U3.15, U4.1
/tmc429_driver_0/~CS_DRIVER_1_B: R7.2, SS2.5, U3.13, U7.1
/tmc429_driver_0/~CS_DRIVER_2_B: R12.2, SS3.5, U3.11, U10.1
/tmc429_driver_0/~ENABLE_0_B: SS1.8, U3.16
/tmc429_driver_0/~ENABLE_1_B: SS2.8, U3.14
/tmc429_driver_0/~ENABLE_2_B: SS3.8, U3.12
GND: C1.2, C2.2, C3.2, C4.2, C5.2, C6.2, C7.2, C8.2, C9.2, C10.2, C11.2, C12.2, C13.2, C14.2, C15.2, C16.2, C17.2, C18.2, C19.2, C20.2, C21.2, C22.2, C23.2, CLK1.2, MDB1.GND, P1.2, R4.2, R6.2, R9.2, R11.2, R14.2, R16.2, REG1.2, SS1.10, SS1.16, SS2.10, SS2.16, SS3.10, SS3.16, U1.4, U1.6, U1.23, U1.25, U1.PAD, U2.3, U3.1, U3.10, U3.19, U4.3, U5.2, U6.5, U7.3, U8.2, U9.5, U10.3, U11.2, U12.5
VAA: C2.1, C6.1, C7.1, C12.1, C13.1, C18.1, C19.1, D1.2, P1.1, REG1.1, SS1.9, SS2.9, SS3.9
VDD: D1.1, MDB1.VDD

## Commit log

2017-03-31 Initial commit.
    [bom_pcb.csv, bom_pcb_add.csv, digikey_order_pcb.csv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]
2017-03-31 Added files from stepper_controller_3x2.
    [stepper.sch, stepper_controller_5x3.kicad_pcb, stepper_controller_5x3.sch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]
2017-03-31 Made some changes.
    [stepper.sch, stepper_controller_5x3.sch, tmc429_tmc26x.sch]
2017-03-31 Made changes.
    [stepper.sch, stepper_controller_5x3.sch, tmc429_tmc26x.sch]
2017-06-15 tmc26x -> driver.
    [stepper_controller_5x3.sch, tmc429_driver.sch]
2017-06-15 Resized component.
    [stepper.sch, stepper_controller_5x3.sch, tmc429_driver.sch]
2017-06-16 Progress towards v1.0.
    [bom_pcb.csv, digikey_order_pcb.csv, stepper.sch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]
2017-06-19 Finished v1.0.
    [bom_pcb.csv, bom_pcb_add.csv, digikey_order.csv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]
2017-09-13 Updated 0.1uF capacitors.
    [bom_pcb.csv, digikey_order.csv, digikey_order_pcb.csv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]
2017-10-23 Progress toward v1.1.
    [stepper.sch, stepper_controller_5x3.dsn, stepper_controller_5x3.kicad_pcb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]
2017-10-24 More progress towards v1.1.
    [stepper.sch, stepper_controller_5x3.kicad_pcb, stepper_controller_5x3.sch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]
2017-10-25 Finished version 1.1.
    [bom_pcb.csv, bom_pcb_add.csv, digikey_order.csv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]
2018-01-08 Updated to v4.
    [stepper.sch, stepper_controller_5x3.sch, tmc429_driver.sch]
2018-05-16 Preparing documentation.
    [bom_pcb.csv, bom_pcb_add.csv, digikey_order.csv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]
2018-05-17 Updated documentation.
    [digikey_parts.csv]
2018-08-12 Marked extra Teensy 3.5 Pins.
2019-03-25 Changes towards v1.2
    [stepper.sch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]
2019-03-28 More progress towards v1.2
    [stepper.sch, stepper_controller_5x3.sch, tmc429_driver.sch]
2019-04-01 Test routing of new version
    [stepper.sch, stepper_controller_5x3.dsn, stepper_controller_5x3.kicad_pcb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]
2019-04-02 Update documentation
    [digikey_order.csv, digikey_parts.csv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]
2019-04-02 Remove superfluous file
    [tmc429.sch]
2019-04-11 Add limit switch filter capacitors
    [digikey_order.csv, digikey_parts.csv, stepper.sch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]
2019-04-11 Fixed broken schematic.
    [stepper.sch]
2019-04-11 footprints: -> stepper_controller_5x3:
    [stepper_controller_5x3.kicad_pcb, tmc429_driver.sch]
2021-09-21 Remove ignored files
    [stepper_controller_5x3.dsn]
